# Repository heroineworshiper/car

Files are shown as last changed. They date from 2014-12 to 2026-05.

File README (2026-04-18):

3D printed truck

Copyright (C) 2012-2025 Adam Williams <broadcast at earthling dot net>

This program is free software; you can redistribute it and/or modify
it under the terms of the GNU General Public License as published by
the Free Software Foundation; either version 2 of the License, or
(at your option) any later version.

This program is distributed in the hope that it will be useful,
but WITHOUT ANY WARRANTY; without even the implied warranty of
MERCHANTABILITY or FITNESS FOR A PARTICULAR PURPOSE.  See the
GNU General Public License for more details.

You should have received a copy of the GNU General Public License
along with this program; if not, write to the Free Software
Foundation, Inc., 59 Temple Place, Suite 330, Boston, MA  02111-1307  USA

What you'll find here:

=============================================================================
3D printed truck

The current camera mounting gear is manely part of truckcam

arm_truck2.c, arm_truck2.h: the 3D printed truck firmware

settings.car: settings file that goes in /sdcard/truck/

antler3.FCStd: antlers  
    Print with .8mm nozzle .32 layer height, 20% infill
    Print in halves.  Glue a half to a tab to make a right angle.
    Then glue the other half to the right angle.

antler5.FCStd: container attachments for antlers

a1323.pcb: hall effect sensor board for motor sensor

l6234.pcb: H bridge board for motor

l6234c.FCStd: bracket which presses the L6234 board against the aluminum
heat sink/angle rod
    print with .8mm nozzle .32mm layer
    use pen spring & lock nut to press 1 side.  Use self tapper for the other side.

imu4.pcb: IMU for 3D printed truck

cring.FCStd: OBSOLETE failed retaining ring for the motors.
    .4mm nozzle
    .2mm layer height out of PETG
    no cooling fan

tire2.FCMacro: OBSOLETE generate procedural tire.
    requires creating a rigid body 1st
    .28mm layer height
    .8mm line width
    1.6mm wall thickness
    1.4mm top/bottom thickness
    100% infill
    no support
    230 printing temp
    0 bed temp
    20mm print speed
    no retraction

front_tire4.FCStd: front tire for soft TPE
    Import STL into blender
    Rename the object "Tire"
    Run helix.py to make it a helix
    Export new layers as an STL file
    .8mm nozzle.  .32 mm layer height stretched to .36 after slicing.
    The wheels must be wider to compensate for the stretching.
    left & right must be mirror images

front_wheel2.FCStd: latest front wheel
    modeled for a .4mm nozzle
    .32 layer height

glasses.FCStd: rear view glasses for testing leash mode
    .32mm layers .4 nozzle

leash13.FCStd: Latest leash enclosure
    no support for string hole
    support for base.  Melt it off.
    .2mm layers .4mm nozzle
    Ball bearings
    Use 5mV/G hall effect sensors
    Keep components near the axle to reduce inertia.

leash.c: leash firmware

leash_test.c: leash tester

light3.FCStd: nose mount for LED lightbulb

offroad2.stl: OBSOLETE offroad rear tire for hard TPU
    print with .4mm nozzle
    TPU
    .32mm layer height
    260C
    left & right must be mirror images

offroad3.stl: offroad rear tire for soft TPE
    print with .8mm nozzle 260C
    All .32mm layer height stretched to .36
    Set Z seam to "shortest" to overcome nozzle clogs 
        by printing the longest section of each layer 1st
    Print Initial layer at 10mm/s
    Buildtak bed with no heating or it won't adhere

rear_tire3.FCStd: OBSOLETE rear wheel

rear_wheel2.FCStd: OBSOLETE on-road rear wheel
    print hub cap in PLA 
        .4mm nozzle .32mm layer height for INNER HUB, INNER RING
        .4mm nozzle .2mm layer height for OUTER HUB, OUTER RING
    tire model is a mockup

rear_wheel4.FCStd: most recent off-road rear wheel
    .4mm nozzle .32mm layer height for INNER HUB, INNER RING
    .4mm nozzle .2mm layer height for OUTER HUB, OUTER RING
    change screw_r2 to select m2 or 6-32 farsteners

tire3.stl: OBSOLETE front tire for hard TPU

tire4.stl: front tire for soft TPE
    print with .8mm nozzle
    TPE
    All .32mm layer height stretched to .36mm
    260C
    left & right must be mirror images

tire6.FCMacro: Create layer for the latest rear tire
    Extrude by the layer height .32mm, then export tire.stl
    Then run helix.c to generate a helix by creating discrete layers
        ./helix tire.stl offroad3.stl
    tires must be mirror images or the truck will pull to 1 side

trailer9.FCStd: Towed drogue for aiding video composition.
    .8 nozzle .32 layers

truck_radio3.pcb: remote control TX for camera panner
    - obsolete RX

truck_radio4.pcb: remote control TX for 3D printed truck
    - obsolete RX
    - uses Si4421 for receive + Si4463 for transmit

truck4.pcb: mane board for 3D printed truck

ball_link.FCStd: 
    ball link
    100% infill
    80 deg support
    220C nozzle 0C bed to improve part cooling
    link spacing on both sides: 38.5mm
     - this grows as the wheel forks wear down
    use pliers when threading to avoid delamination
    grind a flat in the metal rod to aid the pliers
    heat the PLA & shape it with tweezers to get it to conform
    TODO: expand the opening & use heat to close it

bumper2.FCStd:
    bumper for the front of the angle rods
    print in TPU, .8 nozzle, .32 layers

container4.FCStd:
    print masks have to be booleaned with panels in Blender
    Must tweek boolean so all bits appear
    Handle doesn't attach right on the print mask seam.  It attaches 1/2 a triangle behind it.

    Use PLA, 100% infill, 220C/60C on glass
    Use .24mm on 1st 4 layers & .2 on later layers with fixcura.py.
    Ideally would use .32 on later layers.

    TODO: Create fiducials for aligning handle.
        2nd row of front mounting holes for nose.
        paper or foam gasket too fill gaps under container
        flat barrier under container

container.FCMacro:
    scripts for creating the container

corners.FCStd:
    top front corners with light positions
    print corner & support
    .4 nozzle, .2 layers 260C
    Use brim to aid adhesion to glass

lid.FCStd: container lid for waterproofing, cooling  

handle.FCStd:
    collapsing handle for the latest container & 14mm diameter carbon fiber
    print bearing + collars for camera pole or a wide collar without camera pole

rear_light2.FCStd:
    bumper for rear lights
    aluminum heat sink hangs off 2 screws
    .4 nozzle, .2 layers 260C TPU

plot.py: 
    plot steering filters

phone4.FCStd:
    wiko 3 phone

phone6.FCStd:
    moto phone holster to be printed in TPU & welded with soldering iron
    use scotch around the opening
    .4mm nozzle
    .2mm layer

radio_box3.FCStd:
    container for radio modules & switches.
    print without support
    print latches flat & glue on

speaker.FCStd: speaker holder
    .4mm .32 layers

tool.FCStd: socket wrench for 6-32 locknuts

tool2.FCStd: socket wrench for 4-40 locknuts

traction.FCMacro: create objects for traction

traction.FCStd: traction section
    .8mm nozzle, .32mm layer height, no support
    battery walls:
        print fillet side up so the laminations are the right way.
    latch pivot
    back, front, door:
        fillet on top
        support to base only, 80 degrees
    bottom, electronicals:
        no support
    right side:
        side cutout
        hinge
        captive nuts

    union for both sides (motor support | side cutout) & side mask
    union for both sides (motor support & motor mask)
    union for both sides (motor support | side cutout) & bottom mask
     - boolean error causes it to not print mirrored side.  Use cura mirror instead.
    union for both sides (motor support | side cutout) & top mask

    TODO: captive nuts for angle rod farsteners
        round all wire passages

Truck.studio2: the phone app
    Installing it requires creating /sdcard/truck & copying settings.car to it

steering.FCMacro:
    create objects for steering

steering2.FCStd: OBSOLETE steering section with 10 deg caster

steering3.FCStd: steering with 20 deg caster
    print with 0.8mm nozzle 
    .32mm layer height
    shield2
    vertical part
     - print sideways
     - ream holes with 3mm bit
    wheel mount003
    servo plate008
    bushing, bushing001
     - .4 nozzle .32mm layer
     - hard TPU
    wheel mount003

rear_wheel.FCStd: OBSOLETE motor wheel coupling
    print with 0.8mm nozzle
    .8mm line width
    .32mm layer height
    ultimaker project: front_wheel.3mf, rear_wheel.3mf
    print unions with print mask
    print rings
    no support

motor4.FCStd: motor mount
    Use 2.5mV/G hall effect sensors.
    The following use .8mm nozzle, .32 layer height, 100% infill
    SHROUD - support with 80deg overhang
        - not mirror images
    SOCK out of TPU
    CLAMPS out of PLA
    MOTOR PLATE - no support, PETG

    SENSOR PLATE
        100% infill
        .4mm nozzle, .2mm layer
    MAGNET HOLDER
        PETG
        no support, 100% infill
        .4mm nozzle .32mm layer
        Heat to thread set crew & fit magnet
    GASKET:
        TPU .4mm nozzle .32mm layer

car_remote.FCMacro:
    create objects for car_remote & cam_remote

car_remote4.FCStd: remote control for vehicle
    Use 2.5mV/G hall effect sensors
    disable support for the top & bottom
    use support only for the joysticks
    no ironing
    .4mm nozzle
    .6mm top/bottom thickness
    1.2mm wall thickness
    skirt
    use timelapse mode to improve columns
    bottom, top:
        expand all clones
        select base of mirror
        select visible objects
        no support
        print with outside facing the bed
    steering pivot, throttle pivot:
        use support from magnet holder to bed
        Z seem on thicker walls
    steering lever, throttle lever:
        flat side down
    covers for power, increase speed, decrease speed:
        no support
        with wide part facing bed
    sock top/bottom: must clean the inside before welding

car_remote.X: remote control firmware

arm_receiver.c: oversampling, high quality receiver

charger3.FCStd: charging stand for a Qi charger
    print with .4mm nozzle, .4mm line width, no support
    M2 self tappers

confuser.FCStd: jetson nano enclosure

nose2.FCStd: nose cone
    print with .8mm nozzle, .20mm layers on glass
    raise & lower print mask Z to subdivide the top panel
nose.FCMacro: create isogrids for the nose cone

filament budget for traction module:
motor mounts: 39g * 2
bottom: 55g
sides: 49g * 2
front, rear, door, battery walls:  55g

===========================================================================

Carbon fiber farsteners for a fixed gopro

Key files:

isogrid_plane.FCMacro:
    create isogrids for cam_remote, car_remote, & cam_gearbox.FCStd

clamshell.FCMacro:
    create walls for cam_remote, car_remote OBSOLETE

gopro_case2.FCStd: case for a gopro 7
    collars, interfaces for CF rod
    print with support everywhere, lesser overhangs facing up
    skirt adhesion
    .2mm layers .4mm nozzle

gopro.FCStd
    top endpiece for carbon fiber
        print with laminations distributing plasic flex along right angles
        support everywhere
    
    bottom endpiece

    both endpieces need "outer shroud" + "bolt loop"
        print with laminations perpendicular to shaft
    
    4 * "inner shroud slice" for the top & bottom endpieces
        print with laminations distributing plastic flex along curves

    bottom needs "base"
    
    top needs "cam"

=============================================================================

Camera panning mount:

This is used together with countreps to get automatic tracking, motion
control.

arm_cam.c: camera motor receiver using STM32.
    Build with make cam.bin
    Uses a brushless servo hacked into a stepper motor with the servo/ firmware.

arm_cam.c.l6234: camera motor receiver using an L6234 
    to drive a stepper motor.

cam_remote.pcb, cam.pcb: electronicals

cam_remote.X: camera remote control firmware
    Build with mplab_ide

cam_gearbox.FCStd: OBSOLETE
    hobby motor as a stepper motor
    4.5:1 gear reduction for panning motor
    walls have to be printed with .4mm thick tops & bottoms
        to get smooth surfaces
    print pinion with gear on bottom & no support
    install pinion with hex facing motor hex

cam_remote2.FCStd:
    TODO: 5mm longer for new battery
        guard for power switch

    remote control for camera panner
    no ironing
    no horizontal expansion
    .4mm nozzle
    .8mm top/bottom thickness
    1.2mm wall thickness
    support with 60 deg overhang angle
    skirt
    60C bed temp
    support to bed only except for top & bottom
    top, bottom:
        block support over all except edges with switch covers
        print with outside facing the bed
        .8mm top & bottom thickness to get smooth 2mm sheets
        print top with spring holder but not spring
    lever, steering:
        print with support on flatter side
        don't print magnets
    power, increase, decrease cover:
        print with no support
    top switch cover, bottom switch cover:
        support everywhere

gopro_rightangle.FCStd: OBSOLETE handle end pieces
    cf collar - print 2 for the handle
        100% infill

    solid right angle coupling between 2 carbon fiber rods
    print with no support
    print with laminations distributing plastic flex along curves

    attachment + attachment mirror are required

gopro_motor.FCStd: OBSOLETE
    coupling of CF to direct drive motor for panning without a gearbox
    must print with
        4 * "inner shroud slice"
         - TODO: make hole for motor shaft & make base wider to compensate for lost material
        "outer shroud" + "bolt loop"

servo/:
    Firmware for turning a brushless TS-940-HG servo into a stepper motor.
    The project file is servo/motor.wsp.  The output hex file is servo/motor.hex.
    Must be built with the silabs IDE & flashed with the blheli tool.
    https://www.silabs.com/developers/8-bit-8051-microcontroller-software-studio
    http://www.olliw.eu/2012/owsilprog/#firmware

shroud.FCStd: OBSOLETE
    the shroud for a direct drive panning motor
    tube segment was created with 
    ./tube shroud.stl 30 60 0 16
    print with .4mm line width
    205C filament 60C bed

15mph/1185rpm on 12V with no load
4248 traction motors with 108mm tires:
20 turns 26 AWG

272rpm on 10V with no load
70 turns * 32 AWG

Maximum windings: 25 turns * 26AWG
75 turns * 32 AWG

RPM = C constant * V voltage * A wire cross section

========================================================================
OBSOLETE files:

arm_car.c: 2 wheel robot driven by direct drive, sensored brushless motors

arm_cc1101.c: 433Mhz radio library for the ARM

arm_truck.c, arm_truck.h: the lunchbox firmware

arm_xbee.c: xbee library for the ARM

car.s: vehicle firmware for the G buggy

car_remote.s: orginal assembly language remote for CC1101 & XBee

car_remote.X: 3D printed vehicle remote control

car_receive.X: low quality RS232 receiver

car_remote.X.bak: failed remote for the XBee with frequency hopping

freq_hops.ods: frequency hopping plot to aid in spreading the frequencies

fuse.X: a software fuse for testing motors

truck3.pcb: last layout for the tamiya board

uwb.X, dw3000.pcb, dw3220.fp, uwb_test.c: failed UWB experiment with the
DW3221

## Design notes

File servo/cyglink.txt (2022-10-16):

"Z:\servo\motor.obj"  TO "Z:\servo\motor" RS(256) PL(68) PW(78)

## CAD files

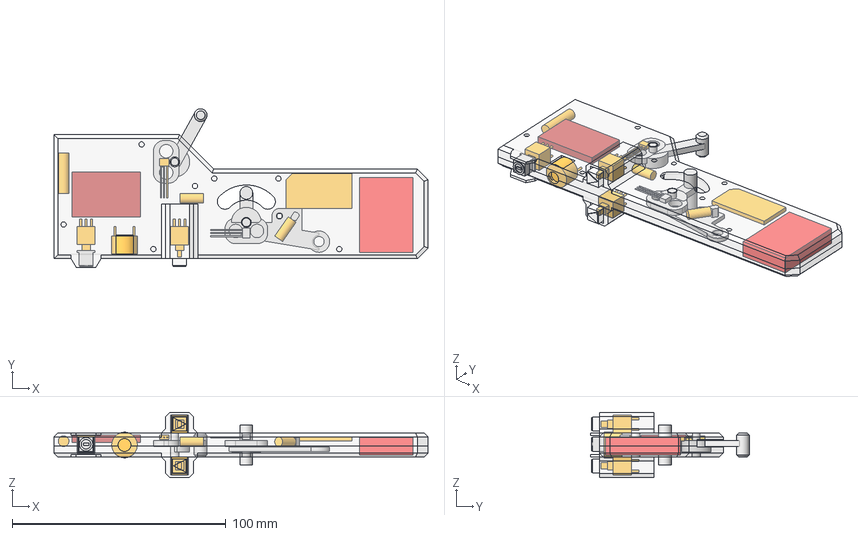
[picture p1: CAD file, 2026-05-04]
car_remote4.FCStd
175.0 x 74.2 x 30.6 mm
rect
wheel shaft
handle
lever opposition
magnet holder001
radio
wheel shaft001
lever opposition001
magnet holder003
wheel shaft002
spring003
up icon
switch cover
down icon
switch cover001
power switch001
down button
up button
decrease speed cover001
hall
top001
bottom001
hall001
speaker001
power switch cap002
throttle lever pivot002
increase speed cover (Mirror #6)
steering lever pivot001
spring
battery001
inductor (X set by charger clearance)
charger board001
antenna (clear from inductor)001

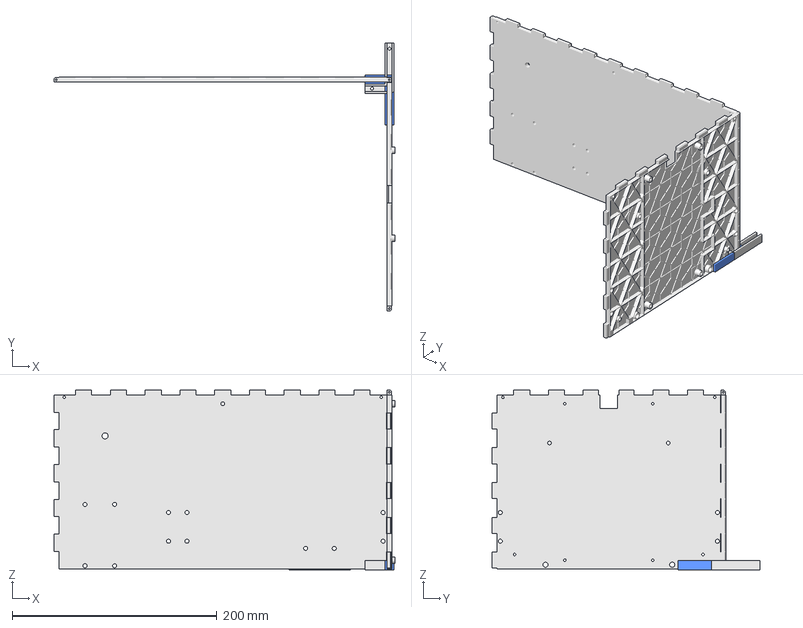
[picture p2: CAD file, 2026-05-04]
rear_light2.FCStd
333.4 x 261.6 x 175.7 mm
rear corner
Body (Mirror #2)
side

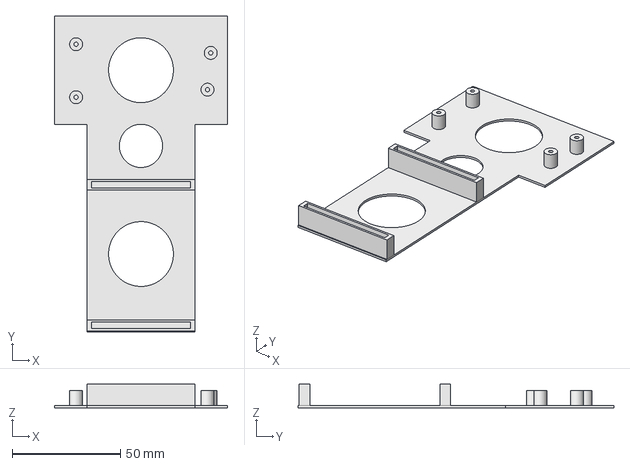
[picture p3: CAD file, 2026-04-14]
charger3.FCStd
80.0 x 146.0 x 11.0 mm

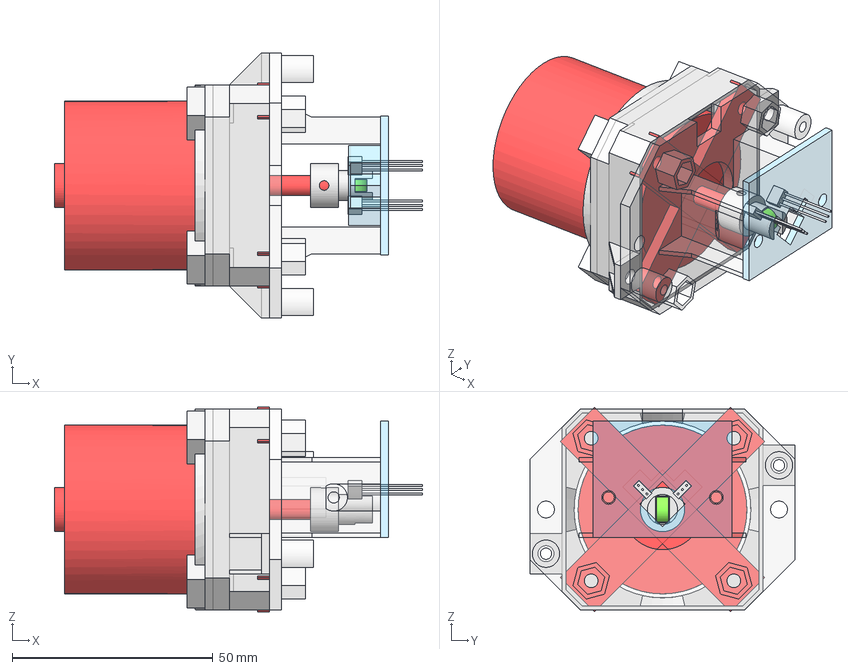
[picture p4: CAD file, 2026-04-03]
motor4.FCStd
91.6 x 66.0 x 50.9 mm
motor
sensor plate003
magnet004
gasket
clamps
shroud001
firewall
halls
magnet holder

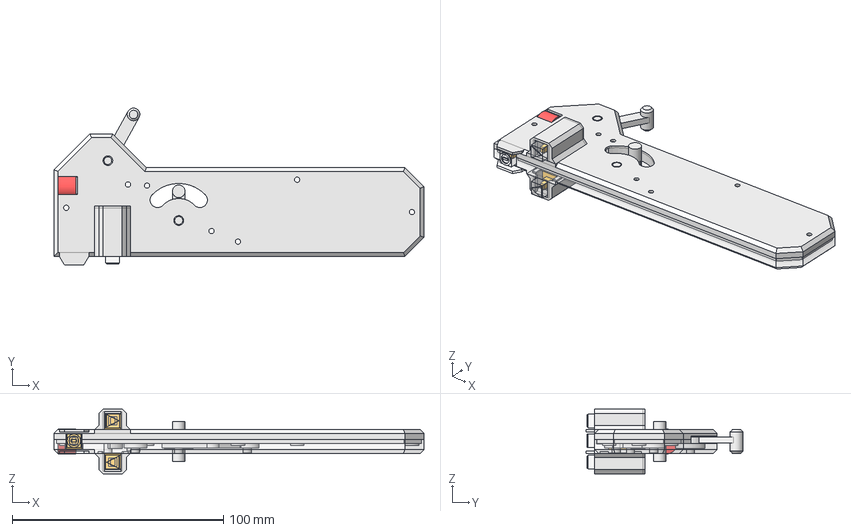
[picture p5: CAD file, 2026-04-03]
car_remote3.FCStd
175.0 x 74.2 x 30.6 mm
hinge
spring stop001
rect
wheel shaft
handle
lever opposition
magnet holder001
wheel shaft001
lever opposition001
magnet holder003
wheel shaft002
spring003
hinge001
spring stop002
spring004
power icon001
power switch cover
up icon
switch cover
down icon
switch cover001
speaker
speaker pin001
speaker pin
power switch001
down button
up button
decrease speed cover001
increase speed cover001
hall
top001
bottom001
hall001

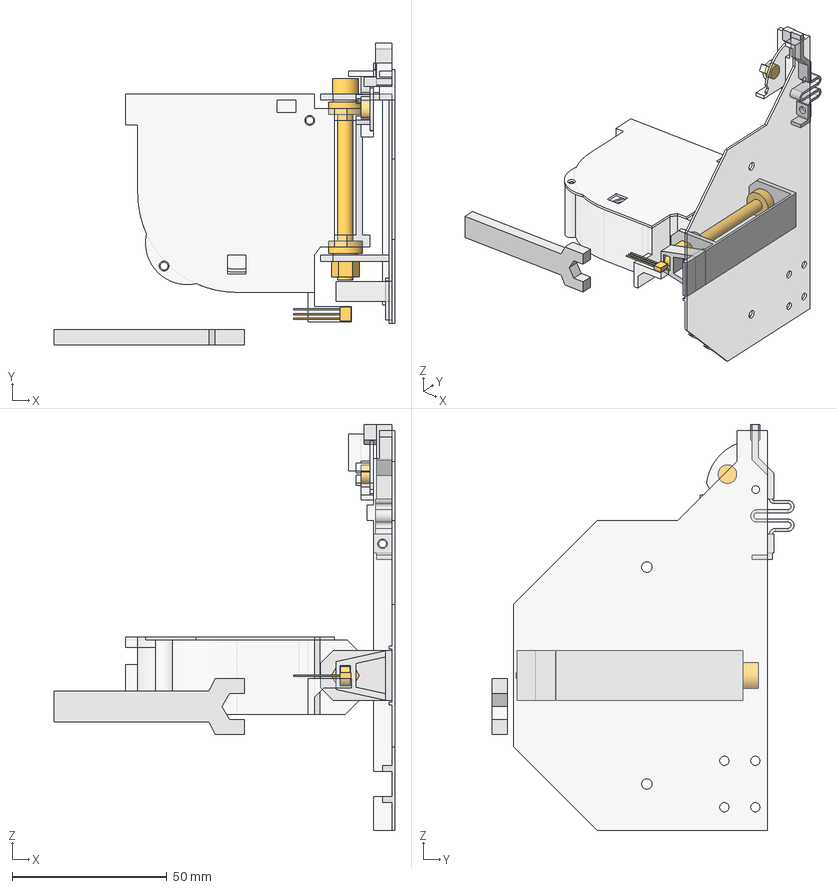
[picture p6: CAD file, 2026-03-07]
leash13.FCStd
110.0 x 97.5 x 131.0 mm
panel
hall006
bearing001
bearing002
bolt001
nut001
magnet
base005
cover001
frame001
latch002
magnet holder002
magnet001
spring
wrench

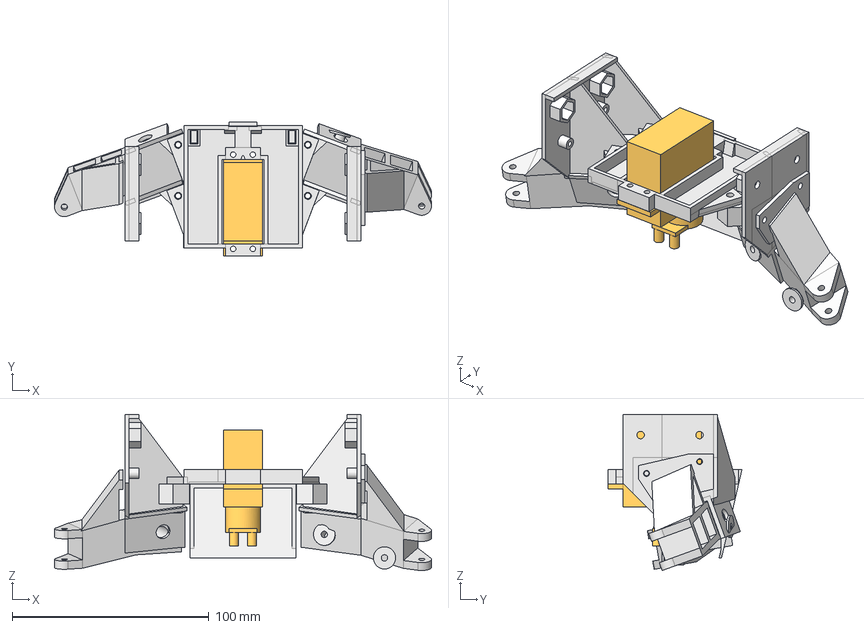
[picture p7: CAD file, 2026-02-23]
steering3.FCStd
191.8 x 68.2 x 79.4 mm
servo
wheel vertical mirror001
wheel fork006
wheel stopper001 (Mirror #11)
shield2
angle rod002
bushing
bushing001
wheel mount003
bushing002
bushing003
servo plate008

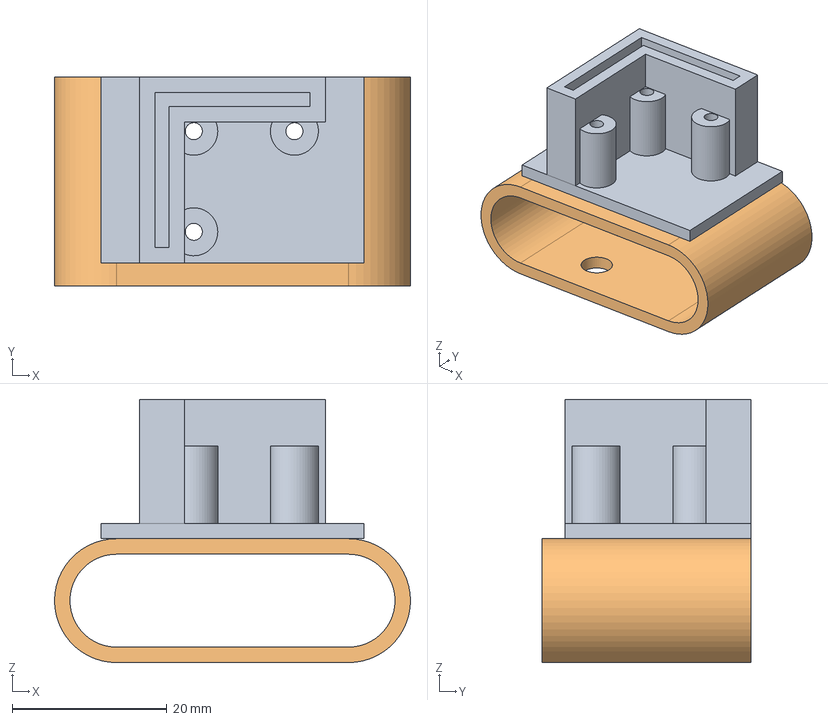
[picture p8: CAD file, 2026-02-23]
bumper2.FCStd
46.0 x 27.0 x 34.0 mm
glove003
bumper003

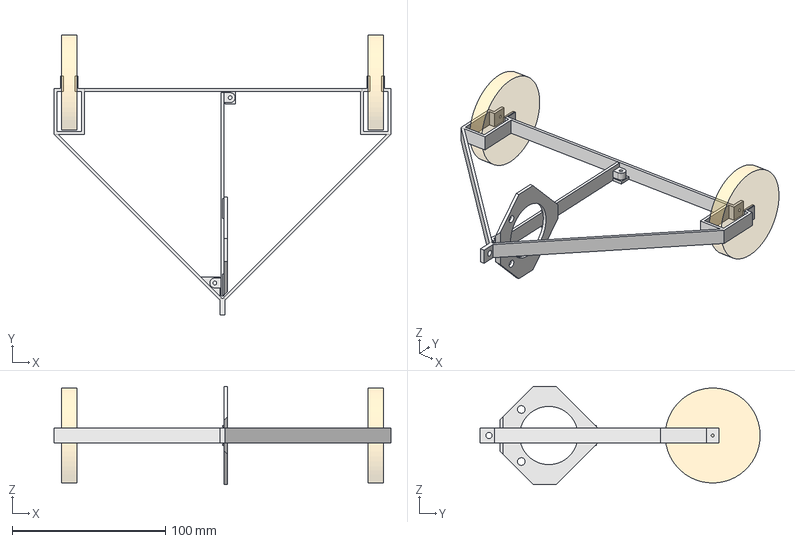
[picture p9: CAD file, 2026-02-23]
trailer9.FCStd
220.0 x 183.0 x 64.0 mm
wheel001
wheel002
frame
skid
center

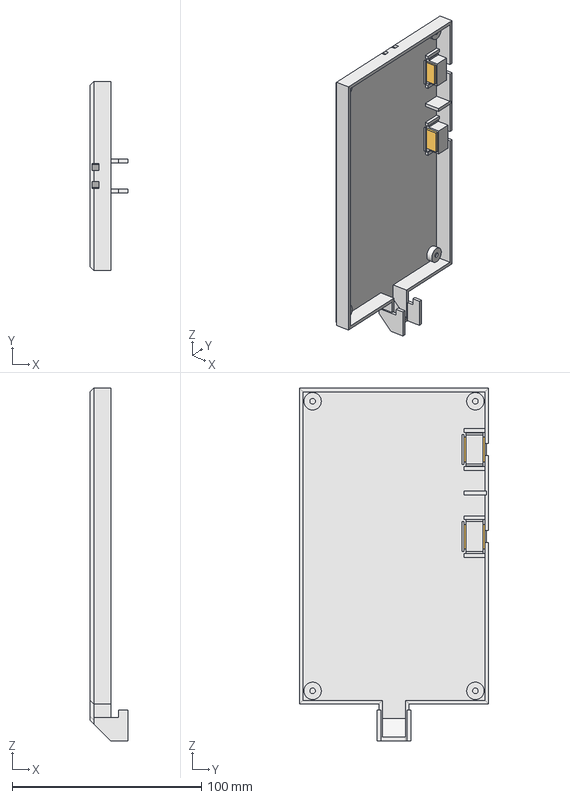
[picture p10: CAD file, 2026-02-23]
radio_box3.FCStd
20.0 x 100.0 x 186.5 mm
radio_box
switches001
strap
strap001
stringer031
latch002
latch001 (Mirror #1)

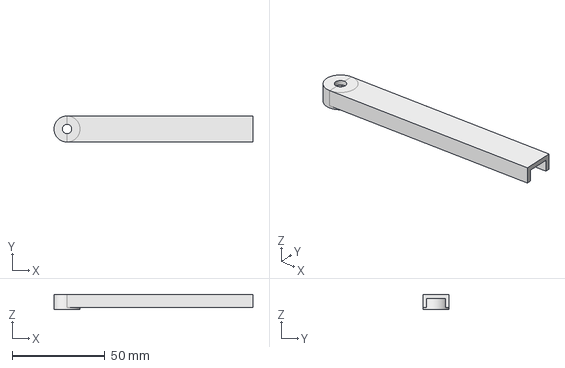
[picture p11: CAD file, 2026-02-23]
tool.FCStd
107.0 x 14.0 x 8.00 mm

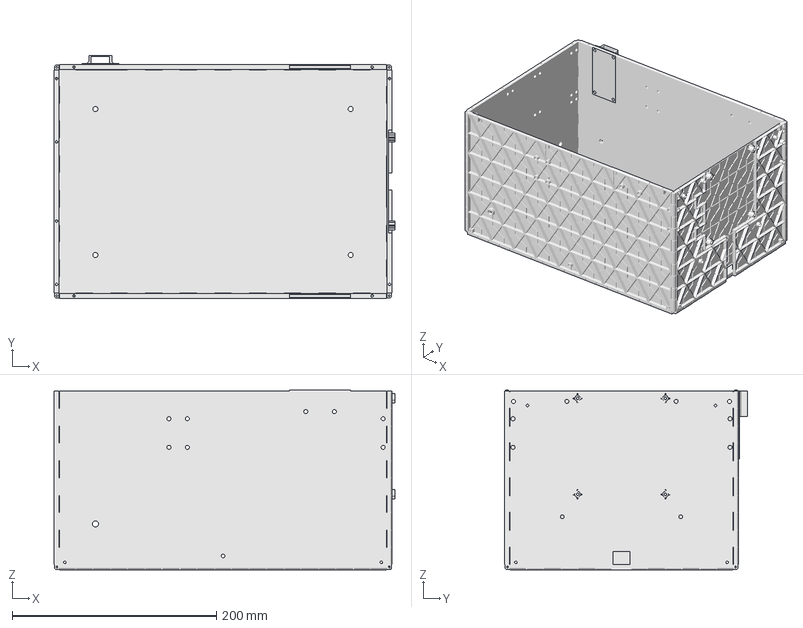
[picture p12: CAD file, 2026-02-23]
antler5.FCStd
334.0 x 238.0 x 176.0 mm
doubler001
panel
hook
container3

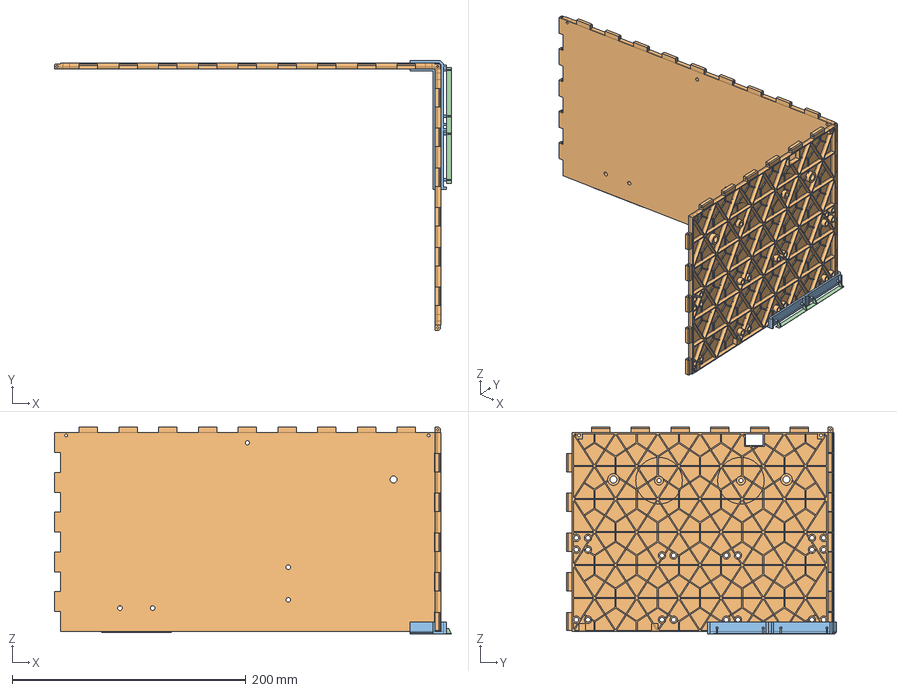
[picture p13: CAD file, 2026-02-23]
corners.FCStd
339.6 x 230.6 x 176.7 mm
corner
support004

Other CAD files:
cam_remote.X/dist/default/production/cam_remote.X.production.obj
servo/motor.OBJ
cam_remote.X/dist/default/production/cam.X.production.obj
servo/motor.c.step
servo/F330_Blinky.OBJ
antler.FCStd
antler2.FCStd
antler3.FCStd
antler4.FCStd
ball_link.FCStd
bottom_corner.FCStd
bumper.FCStd
cam_gearbox.FCStd
cam_remote.FCStd
cam_remote2.FCStd
car_remote.FCStd
car_remote2.FCStd
charger.FCStd
charger2.FCStd
confuser.FCStd
connector.FCStd
corners2.FCStd
cring.FCStd
extruder.FCStd
front_corner2.stl
front_tire.FCStd
front_tire2.FCStd
front_tire3.FCStd
front_tire4.FCStd
front_wheel.FCStd
front_wheel2.FCStd
glasses.FCStd
gopro.FCStd
gopro_case.FCStd
gopro_case2.FCStd
gopro_motor.FCStd
gopro_rightangle.FCStd
handle.FCStd
isogrid_test.FCStd
knob.FCStd
l6234.FCStd
l6234b.FCStd
l6234c.FCStd
leash11.FCStd
leash4.FCStd
leash5.FCStd
leash8.FCStd
leash9.FCStd
lid.FCStd
light.FCStd
light2.FCStd
light3.FCStd
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

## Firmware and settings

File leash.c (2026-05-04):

/*
 * Smart leash
 * Copyright (C) 2022-2025 Adam Williams <broadcast at earthling dot net>
 * 
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
 */

// Plug in the ISP programmer
// make leash.hex
// make leash_fuse
// make leash_isp

// Arduino ISP to leash:
// GND - GND
// 13 - CLK
// 12 - MISO
// 11 - MOSI
// 10 - RESET


#define F_CPU 8000000L

#include <stdint.h>
#include <inttypes.h>
#include <avr/io.h>
#include <avr/pgmspace.h>
#include <avr/interrupt.h>
#include <avr/wdt.h>

#define HZ 125
#define FRACTION 256
#define LED_ON PORTB &= ~(1 << PORTB5);
#define LED_OFF PORTB |= (1 << PORTB5);
#define LED_TOGGLE PORTB ^= (1 << PORTB5);
#define LED_DOWNSAMPLE 15

#define BAUD 115200L

#define ENCODER_CENTER 128
#define ENCODER_THRESHOLD 8
#define ON_THRESHOLD 100

#define ENCODER_START 0
#define ENCODER0_LOW 1
#define ENCODER1_LOW 2
#define ENCODER0_HIGH 3
#define ENCODER1_HIGH 4
int8_t encoder_state = ENCODER_START;
int8_t prev_encoder = ENCODER_START;
int16_t encoder_counts = 0;
uint8_t debug_count = 0;

uint16_t enable_accum = 0;
uint16_t encoder0_accum = 0;
uint16_t encoder1_accum = 0;
uint16_t angle_accum = 0;
uint8_t enable_adc = 0;
uint8_t encoder0_adc = 0;
uint8_t encoder1_adc = 0;
uint16_t angle_adc = 0;
uint8_t encoder_count = 0;
uint8_t angle_count = 0;
uint8_t enable_count = 0;
#define ENCODER_OVERSAMPLE 1
#define POT_OVERSAMPLE 32
#define ENABLE_OVERSAMPLE 32
uint8_t tick;
uint8_t led_count = 0;

// byte stuffing for UART
#define START_CODE 0xff
#define ESC_CODE 0xfe

#define UART_SIZE 64
uint8_t uart_buffer[UART_SIZE];
uint8_t uart_used = 0;
uint8_t uart_write_ptr = 0;
uint8_t uart_read_ptr = 0;

#define bitRead(value, bit) (((value) >> (bit)) & 0x01)
#define bitSet(value, bit) ((value) |= (1UL << (bit)))
#define bitToggle(value, bit) ((value) ^= (1UL << (bit)))
#define bitClear(value, bit) ((value) &= ~(1UL << (bit)))
#define bitWrite(value, bit, bitvalue) (bitvalue ? bitSet(value, bit) : bitClear(value, bit))

#define CLAMP(x, y, z) ((x) = ((x) < (y) ? (y) : ((x) > (z) ? (z) : (x))))
#define MAX(x, y) ((x) > (y) ? (x) : (y))
#define MIN(x, y) ((x) < (y) ? (x) : (y))
#define ABS(x) ((x) < 0 ? (-(x)) : (x))



// send data to the UART buffer
void send_uart(uint8_t *text, uint8_t size)
{
	uint8_t i;
	for(i = 0; uart_used < UART_SIZE && i < size; i++)
	{
		uart_buffer[uart_write_ptr++] = text[i];
		uart_used++;
		if(uart_write_ptr >= UART_SIZE) uart_write_ptr = 0;
	}
}

void send_uart1(uint8_t c)
{
    if(uart_used < UART_SIZE)
    {
        uart_buffer[uart_write_ptr++] = c;
	    uart_used++;
	    if(uart_write_ptr >= UART_SIZE) uart_write_ptr = 0;
    }
}

void print_text(char *text)
{
	uint8_t i;
	for(i = 0; uart_used < UART_SIZE && text[i] != 0; i++)
	{
		uart_buffer[uart_write_ptr++] = text[i];
		uart_used++;
		if(uart_write_ptr >= UART_SIZE) uart_write_ptr = 0;
	}
}

void print_number_nospace(int number)
{
	char string[8];
	char *ptr = string;
	if(number < 0)
	{
		*ptr++ = '-';
		number = -number;
	}

	if(number >= 10000) *ptr++ = '0' + (number / 10000);
	if(number >= 1000) *ptr++ = '0' + ((number / 1000) % 10);
	if(number >= 100) *ptr++ = '0' + ((number / 100) % 10);
	if(number >= 10) *ptr++ = '0' + ((number / 10) % 10);
	*ptr++ = '0' + (number % 10);
	*ptr = 0;
	print_text(string);
}

void print_number(int number)
{
    print_number_nospace(number);
	print_text(" ");
}


void print_fixed(int16_t number)
{
    print_number_nospace(number / FRACTION);
	char string[8];
	if(number < 0) number = -number;
    uint8_t fraction = number % FRACTION;
    string[0] = '.';
    fraction = fraction * 100 / FRACTION;
    string[1] = '0' + (fraction / 10);
    string[2] = '0' + (fraction % 10);
    string[3] = ' ';
    string[4] = 0;
	print_text(string);
}


void encode_serial(uint8_t c)
{
    if(c == START_CODE || c == ESC_CODE)
    {
        send_uart1(ESC_CODE);
        send_uart1(0xff ^ c);
    }
    else
        send_uart1(c);
}

void encode_start()
{
    send_uart1(START_CODE);
}

void handle_serial()
{
	if(uart_used) 
	{
	    if(bitRead(UCSR0A, UDRE0)) 
	    {
			bitSet(UCSR0A, UDRE0); 
			UDR0 = uart_buffer[uart_read_ptr++]; 
			if(uart_read_ptr >= UART_SIZE) uart_read_ptr = 0; 
			uart_used--; 
	    }
	}
}

void init_serial()
{
	uint16_t baud_setting = (F_CPU / 4 / BAUD - 1) / 2;
	UBRR0H = baud_setting >> 8;
	UBRR0L = baud_setting & 0xff;
	UCSR0A = (1 << U2X0);
	UCSR0C = (1 << UCSZ01) |
		(1 << UCSZ00);
	UCSR0B = (1 << RXCIE0) |
		(1 << TXEN0);
//         |
//		(1 << RXEN0);
}



void handle_encoder()
{
    if(encoder1_adc <= ENCODER_CENTER - ENCODER_THRESHOLD)
    {
        encoder_state = ENCODER1_LOW;
    }
    else
    if(encoder1_adc >= ENCODER_CENTER + ENCODER_THRESHOLD)
    {
        encoder_state = ENCODER1_HIGH;
    }
    else
    if(encoder0_adc <= ENCODER_CENTER - ENCODER_THRESHOLD)
    {
        encoder_state = ENCODER0_LOW;
    }
    else
    if(encoder0_adc >= ENCODER_CENTER + ENCODER_THRESHOLD)
    {
        encoder_state = ENCODER0_HIGH;
    }
    
    if(encoder_state != prev_encoder)
    {
        if(prev_encoder == ENCODER1_LOW && encoder_state == ENCODER0_LOW ||
            prev_encoder == ENCODER0_LOW && encoder_state == ENCODER1_HIGH ||
            prev_encoder == ENCODER1_HIGH && encoder_state == ENCODER0_HIGH ||
            prev_encoder == ENCODER0_HIGH && encoder_state == ENCODER1_LOW)
            encoder_counts++;
        else
        if(prev_encoder == ENCODER0_LOW && encoder_state == ENCODER1_LOW ||
            prev_encoder == ENCODER1_LOW && encoder_state == ENCODER0_HIGH ||
            prev_encoder == ENCODER0_HIGH && encoder_state == ENCODER1_HIGH ||
            prev_encoder == ENCODER1_HIGH && encoder_state == ENCODER0_LOW)
            encoder_counts--;

        prev_encoder = encoder_state;
    }
}

void main()
{
// disable watchdog
	WDTCSR = 0;
	init_serial();
	print_text("\n\nWelcome to smart leash\n");

// LED/DEBUG
    DDRB |= 1 << DDB5;
    LED_ON

// tick clock prescaler page 108
// CLKio is 32khz
    TCCR0B = 0b00000100;

#define ADMUX_BASE 0b01000000
    ADMUX = ADMUX_BASE;
    ADCSRA = 0b10000111;
// disable digital inputs
    DIDR0 = 0b00001111;
    bitSet(ADCSRA, ADSC);

// enable interrupts
	sei();

 	while(1)
	{
		handle_serial();

// handle tick
        if(bitRead(TIFR0, TOV0))
        {
            bitSet(TIFR0, TOV0);
            tick++;
            if(tick >= HZ / 25)
            {
                tick = 0;
            }
        }

        if(bitRead(ADCSRA, ADIF))
        {
            uint8_t channel = ADMUX & 0xf;
            bitSet(ADCSRA, ADIF);
            
// must read the right byte order to update the registers
            uint8_t low = ADCL;
            uint8_t high = ADCH;
            switch(channel)
            {
                case 0:
                    ADMUX = ADMUX_BASE | 1;
                    encoder0_accum += (high << 8) | low;
                    bitSet(ADCSRA, ADSC);
                    break;
                case 1:
                    ADMUX = ADMUX_BASE | 2;
                    encoder1_accum += (high << 8) | low;
                    bitSet(ADCSRA, ADSC);
                    encoder_count++;

                    if(encoder_count >= ENCODER_OVERSAMPLE)
                    {
                        encoder0_adc = encoder0_accum / ENCODER_OVERSAMPLE / 4;
                        encoder1_adc = encoder1_accum / ENCODER_OVERSAMPLE / 4;
                        encoder_count = 0;
                        encoder0_accum = 0;
                        encoder1_accum = 0;


                        handle_encoder();

//                         debug_count++;
//                         if(debug_count > 10)
//                         {
//                             debug_count = 0;
//                         print_number(encoder0_adc);
//                         print_number(encoder1_adc);
//                         print_number(angle_adc);
//                         print_text("\n");
//                        }
                    }
                    break;
                case 2:
                    ADMUX = ADMUX_BASE | 3;
                    angle_accum += (high << 8) | low;
                    bitSet(ADCSRA, ADSC);

                    angle_count++;
                    if(angle_count >= POT_OVERSAMPLE)
                    {
// scale it to maximize resolution
//                        angle_accum -= 32 * 512;
//                        angle_accum /= POT_OVERSAMPLE;
//                        angle_accum += 128;
// send the entire accumulator
                        angle_adc = angle_accum;
// compress accumulator into 8 bits
//                        angle_adc = angle_accum / POT_OVERSAMPLE / 4;
                        angle_accum = 0;
                        angle_count = 0;

// send to autopilot
                        if(enable_adc >= ON_THRESHOLD)
                        {
                            LED_TOGGLE

                            encode_start();
                            encode_serial(encoder_counts & 0xff);
                            encode_serial(encoder_counts >> 8);
// send the entire accumulator
                            encode_serial(angle_adc & 0xff);
                            encode_serial(angle_adc >> 8);
                            encode_serial(encoder0_adc);
                            encode_serial(encoder1_adc);
                        }
                        else
                        {
// standby
                            encoder_counts = 0;
                            led_count++;
                            if(led_count >= LED_DOWNSAMPLE)
                            {
                                led_count = 0;
                                LED_TOGGLE
                            }
                        }
                    }
                    break;

                case 3:
                    ADMUX = ADMUX_BASE;
                    enable_accum += (high << 8) | low;
                    bitSet(ADCSRA, ADSC);
                    enable_count++;

                    if(enable_count >= ENABLE_OVERSAMPLE)
                    {
                        enable_adc = enable_accum / ENABLE_OVERSAMPLE / 4;
                        enable_accum = 0;
                        enable_count = 0;

// lion readable output
                        print_text("DEBUG: ");
                        print_number(enable_adc);
                        print_number(angle_adc);
                        print_number(encoder0_adc);
                        print_number(encoder1_adc);
                        print_number(encoder_counts);
                        print_text("\n");
                    }
                    break;
            }
        }
    }
}

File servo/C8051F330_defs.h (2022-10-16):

//-----------------------------------------------------------------------------
// C8051F330_defs.h
//-----------------------------------------------------------------------------
// Copyright 2007, Silicon Laboratories, Inc.
// http://www.silabs.com
//
// Program Description:
//
// Register/bit definitions for the C8051F33x family.
// **Important Note**: The si_toolchain.h header file should be included
// before including this header file.
//
// Target:         C8051F330, 'F331, 'F333, 'F334, 'F335
// Tool chain:     Generic
// Command Line:   None
//
// Release 1.4 - 20 AUG 2012 (TP)
//    -Added #define for _XPAGE to provide support for SDCC memory paging
//     (pdata)
// Release 1.3 - 07 AUG 2007 (PKC)
//    -Removed #include "si_toolchain.h". The C source file should include it.
//    -Removed FID and fixed formatting.
// Release 1.2 - 29 SEP 2006 (PKC)
//    -Reformatted header file to enable portable SFR definitions
// Release 1.1 - 11 JAN 2006 (GP)
//    -Converted file to new coding guidelines
//    -Added #defines for interrupt priorities
//    -Added #ifndef/#define to allow multiple includes of file
// Release 1.0
//    -Latest release before new firmware coding standard

//-----------------------------------------------------------------------------
// Header File Preprocessor Directive
//-----------------------------------------------------------------------------

#ifndef C8051F330_DEFS_H
#define C8051F330_DEFS_H

//-----------------------------------------------------------------------------
// Byte Registers
//-----------------------------------------------------------------------------

SI_SFR(P0, 0x80);                        // Port 0 Latch
SI_SFR(SP, 0x81);                        // Stack Pointer
SI_SFR(DPL, 0x82);                       // Data Pointer Low
SI_SFR(DPH, 0x83);                       // Data Pointer High
SI_SFR(PCON, 0x87);                      // Power Control
SI_SFR(TCON, 0x88);                      // Timer/Counter Control
SI_SFR(TMOD, 0x89);                      // Timer/Counter Mode
SI_SFR(TL0, 0x8A);                       // Timer/Counter 0 Low
SI_SFR(TL1, 0x8B);                       // Timer/Counter 1 Low
SI_SFR(TH0, 0x8C);                       // Timer/Counter 0 High
SI_SFR(TH1, 0x8D);                       // Timer/Counter 1 High
SI_SFR(CKCON, 0x8E);                     // Clock Control
SI_SFR(PSCTL, 0x8F);                     // Program Store R/W Control
SI_SFR(P1, 0x90);                        // Port 1 Latch
SI_SFR(TMR3CN, 0x91);                    // Timer/Counter 3 Control
SI_SFR(TMR3RLL, 0x92);                   // Timer/Counter 3 Reload Low
SI_SFR(TMR3RLH, 0x93);                   // Timer/Counter 3 Reload High
SI_SFR(TMR3L, 0x94);                     // Timer/Counter 3 Low
SI_SFR(TMR3H, 0x95);                     // Timer/Counter 3 High
SI_SFR(IDA0L, 0x96);                     // Current Mode Dac0 Low
SI_SFR(IDA0H, 0x97);                     // Current Mode Dac0 High
SI_SFR(SCON0, 0x98);                     // UART0 Control
SI_SFR(SBUF0, 0x99);                     // UART0 Data Buffer
SI_SFR(CPT0CN, 0x9B);                    // Comparator0 Control
SI_SFR(CPT0MD, 0x9D);                    // Comparator0 Mode Selection
SI_SFR(CPT0MX, 0x9F);                    // Comparator0 Mux Selection
SI_SFR(P2, 0xA0);                        // Port 2 Latch
SI_SFR(SPI0CFG, 0xA1);                   // SPI0 Configuration
SI_SFR(SPI0CKR, 0xA2);                   // SPI0 Clock Rate Control
SI_SFR(SPI0DAT, 0xA3);                   // SPI0 Data
SI_SFR(P0MDOUT, 0xA4);                   // Port 0 Output Mode Configuration
SI_SFR(P1MDOUT, 0xA5);                   // Port 1 Output Mode Configuration
SI_SFR(P2MDOUT, 0xA6);                   // Port 2 Output Mode Configuration
SI_SFR(IE, 0xA8);                        // Interrupt Enable
SI_SFR(CLKSEL, 0xA9);                    // Clock Select
SI_SFR(EMI0CN, 0xAA);                    // External Memory Interface Control
SI_SFR(OSCXCN, 0xB1);                    // External Oscillator Control
SI_SFR(OSCICN, 0xB2);                    // Internal Oscillator Control
SI_SFR(OSCICL, 0xB3);                    // Internal Oscillator Calibration
SI_SFR(FLSCL, 0xB6);                     // Flash Scale
SI_SFR(FLKEY, 0xB7);                     // Flash Lock And Key
SI_SFR(IP, 0xB8);                        // Interrupt Priority
SI_SFR(IDA0CN, 0xB9);                    // Current Mode DAC0 Control
SI_SFR(AMX0N, 0xBA);                     // AMUX0 Negative Channel Select
SI_SFR(AMX0P, 0xBB);                     // AMUX0 Positive Channel Select
SI_SFR(ADC0CF, 0xBC);                    // ADC0 Configuration
SI_SFR(ADC0L, 0xBD);                     // ADC0 Low
SI_SFR(ADC0H, 0xBE);                     // ADC0 High
SI_SFR(SMB0CN, 0xC0);                    // SMBus0 Control
SI_SFR(SMB0CF, 0xC1);                    // SMBus0 Configuration
SI_SFR(SMB0DAT, 0xC2);                   // SMBus0 Data
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

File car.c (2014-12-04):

// mane board for passively stable 2 wheeler


// 18f1320
// usb_programmer -p 18f1320 -e
// usb_programmer -p 18f1320 -c 0x300000 1100100000000000
// Internal oscillator
// usb_programmer -p 18f1320 -c 0x300002 0001111100001010
// brownout protection
// usb_programmer -p 18f1320 -c 0x300006 0000000010000001
// low voltage programming disabled
// make car
// usb_programmer -p 18f1320 -z 0 car.hex
// usb_programmer -p 18f1320 -z 0  -r car.hex

// if it randomly crashes, reflash it








#include <pic18fregs.h>
#include <stdint.h>
#include "util.h"

#define CLOCKSPEED 8000000
#define BUFFER_SIZE 8
#define BAUD 9600
// clock jitter is keeping it as low as possible
//#define BAUD_RATE_CODE (CLOCKSPEED / (BAUD * 4) - 1)
#define BAUD_RATE_CODE 208
#define SYNC_CODE 0xe5
#define THROTTLE_PERIOD 32767
// multiply gyro output by this to get steering feedback
//#define AUTO_STEERING_GAIN 4
#define AUTO_STEERING_GAIN 1
// limit for auto steering magnitude
//#define AUTO_STEERING_LIMIT STEERING_PERIOD / 4
#define AUTO_STEERING_LIMIT STEERING_PERIOD / 2
// integral step
#define STEERING_I_STEP 32
#define STEERING_I_LIMIT STEERING_PERIOD / 4
//#define STEERING_I_LIMIT STEERING_PERIOD / 2
// total readings to use for the center calculation
#define GYRO_TOTAL 1024
// maximum range for center calculation
#define GYRO_LIMIT 128
// timer for LED flashing
#define LED_DELAY 64
// timer for packet flashing
#define LED_DELAY2 2
// total readings for each GYRO_RESULT
#define GYRO_OVERSAMPLE_TOTAL 32
// amount heading has to be off to command auto steering voltage
//#define HEADING_DEADBAND 0x0100
#define HEADING_DEADBAND 0x0000
// amount user changes heading in each packet
#define HEADING_CHANGE 0x0200
// enable UART output
//#define DEBUG

// analog range
#define STEERING_MID 0x8000
// deadband
#define STEERING_MIN 0x800
#define STEERING_MAX 0x7f00

#define THROTTLE_MIN 0x100
#define THROTTLE_MAX 0xff00

#define SDO_LAT LATAbits.LATA2
#define SDO_TRIS TRISAbits.TRISA2

#define SCK_LAT LATAbits.LATA3
#define SCK_TRIS TRISAbits.TRISA3

#define CS0_LAT LATBbits.LATB5
#define CS0_TRIS TRISBbits.TRISB5

#define LEFT_FWD_LAT LATBbits.LATB3
#define LEFT_FWD_TRIS TRISBbits.TRISB3
#define LEFT_BWD_LAT LATAbits.LATA1
#define LEFT_BWD_TRIS TRISAbits.TRISA1

#define RIGHT_FWD_LAT LATAbits.LATA7
#define RIGHT_FWD_TRIS TRISAbits.TRISA7
#define RIGHT_BWD_LAT LATAbits.LATA6
#define RIGHT_BWD_TRIS TRISAbits.TRISA6

#define LED_LAT LATAbits.LATA0
#define LED_TRIS TRISAbits.TRISA0


// transfer types
#define WRITE_BURST_FLAG              0x40
#define READ_SINGLE_FLAG              0x80
#define READ_BURST_FLAG               0xC0

// number of frequency channels
#define NUMBER_OF_FCHANNELS      10

// arrays
#define CC1101_PATABLE           0x3E        // PATABLE address
#define CC1101_TXFIFO            0x3F        // TX FIFO address
#define CC1101_RXFIFO            0x3F        // RX FIFO address

// commands
#define CC1101_SRES              0x30        // Reset CC1101 chip
#define CC1101_SFSTXON           0x31        // Enable and calibrate frequency synthesizer (if MCSM0.FS_AUTOCAL=1). If in RX (with CCA):
                                             // Go to a wait state where only the synthesizer is running (for quick RX / TX turnaround).
#define CC1101_SXOFF             0x32        // Turn off crystal oscillator
#define CC1101_SCAL              0x33        // Calibrate frequency synthesizer and turn it off. SCAL can be strobed from IDLE mode without
                                             // setting manual calibration mode (MCSM0.FS_AUTOCAL=0)
#define CC1101_SRX               0x34        // Enable RX. Perform calibration first if coming from IDLE and MCSM0.FS_AUTOCAL=1
#define CC1101_STX               0x35        // In IDLE state: Enable TX. Perform calibration first if MCSM0.FS_AUTOCAL=1.
                                             // If in RX state and CCA is enabled: Only go to TX if channel is clear
#define CC1101_SIDLE             0x36        // Exit RX / TX, turn off frequency synthesizer and exit Wake-On-Radio mode if applicable
#define CC1101_SWOR              0x38        // Start automatic RX polling sequence (Wake-on-Radio) as described in Section 19.5 if
                                             // WORCTRL.RC_PD=0
#define CC1101_SPWD              0x39        // Enter power down mode when CSn goes high
#define CC1101_SFRX              0x3A        // Flush the RX FIFO buffer. Only issue SFRX in IDLE or RXFIFO_OVERFLOW states
#define CC1101_SFTX              0x3B        // Flush the TX FIFO buffer. Only issue SFTX in IDLE or TXFIFO_UNDERFLOW states
#define CC1101_SWORRST           0x3C        // Reset real time clock to Event1 value
#define CC1101_SNOP              0x3D        // No operation. May be used to get access to the chip status byte


// registers

#define CC1101_IOCFG2            0x00        // GDO2 Output Pin Configuration
#define CC1101_IOCFG1            0x01        // GDO1 Output Pin Configuration
#define CC1101_IOCFG0            0x02        // GDO0 Output Pin Configuration
#define CC1101_FIFOTHR           0x03        // RX FIFO and TX FIFO Thresholds
#define CC1101_SYNC1             0x04        // Sync Word, High Byte
#define CC1101_SYNC0             0x05        // Sync Word, Low Byte
#define CC1101_PKTLEN            0x06        // Packet Length
#define CC1101_PKTCTRL1          0x07        // Packet Automation Control
#define CC1101_PKTCTRL0          0x08        // Packet Automation Control
#define CC1101_ADDR              0x09        // Device Address
#define CC1101_CHANNR            0x0A        // Channel Number
#define CC1101_FSCTRL1           0x0B        // Frequency Synthesizer Control
#define CC1101_FSCTRL0           0x0C        // Frequency Synthesizer Control
#define CC1101_FREQ2             0x0D        // Frequency Control Word, High Byte
#define CC1101_FREQ1             0x0E        // Frequency Control Word, Middle Byte
#define CC1101_FREQ0             0x0F        // Frequency Control Word, Low Byte

// page 76
#define CC1101_MDMCFG4           0x10        // Modem Configuration
#define CC1101_MDMCFG3           0x11        // Modem Configuration
#define CC1101_MDMCFG2           0x12        // Modem Configuration
#define CC1101_MDMCFG1           0x13        // Modem Configuration
#define CC1101_MDMCFG0           0x14        // Modem Configuration
#define CC1101_DEVIATN           0x15        // Modem Deviation Setting
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

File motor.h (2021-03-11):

/*
 * 3 phase motor driver from an ESC
 *
 * Copyright (C) 2021 Adam Williams <broadcast at earthling dot net>
 * 
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
 */


#ifndef MOTOR_H
#define MOTOR_H



#ifdef __AVR__


#define F_CPU 16000000L

#include <inttypes.h>
#include <avr/io.h>
#include <avr/pgmspace.h>
#include <avr/interrupt.h>
#include <avr/wdt.h>
#include <util/delay.h>

#endif // __AVR__

#ifdef __x86_64__

#include  <stdint.h>

#endif // __x86_64__

#define bitRead(value, bit) (((value) >> (bit)) & 0x01)
#define bitSet(value, bit) ((value) |= (1UL << (bit)))
#define bitClear(value, bit) ((value) &= ~(1UL << (bit)))
#define bitToggle(reg, bit) ((reg) ^= (1 << (bit)))
#define bitWrite(value, bit, bitvalue) (bitvalue ? bitSet(value, bit) : bitClear(value, bit))
#define bitIsSet(value, bit) ((value) & (1UL << (bit)))
#define bitIsClear(value, bit) (!((value) & (1UL << (bit))))


#define CLAMP(x, y, z) ((x) = ((x) < (y) ? (y) : ((x) > (z) ? (z) : (x))))


// pins for the FETs
#define P_FET1	5
#define P_FET2	7
#define P_FET3	4
#define N_FET1	0
#define N_FET2	1
#define N_FET3	3

// use the PWM input pin for TX if no receive
#define TX_PIN 2
#define TX_PORT PORTD
#define TX_DDR DDRD



// the table played back by the interrupt handler
typedef struct
{
// members have to be volatile to be access by an interrupt handler
// time until the next interrupt
	volatile uint8_t time;
// value of the PORT register
	volatile uint8_t value;
} pwm_table_t;

// temporary table used for calculating the pwm table
typedef struct
{
// time since overflow
	int16_t time;
// Ps to turn off
	uint8_t p_mask;
// Ns to turn on
	uint8_t n_mask;
} event_table_t;


// need 9uS of deadband from P to N
//#define DEADBAND 104  // prescaler 1
//#define DEADBAND 12 // prescaler 2 with 18A Hobbyking
#define DEADBAND 128 // prescaler 2 with 35A Hobbyking

#define DEADBAND2 0 // minimum delay from N to P saves 20mA on 35A

// tweek this to get the right Hz
// need multiple padding events or higher power if period is too high
//#define PERIOD 582  // maximum before overflow prescaler 1 16khz
#define PERIOD 216  // prescaler 2 8khz
//#define PERIOD 108  // prescaler 2 16khz
//#define PERIOD 280  // prescaler 2 6khz


#define MAX_POWER ((int16_t)PERIOD)

#define MIN_POWER 1


void delayMicroseconds(unsigned int us);




#endif

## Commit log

2017-11-06 throttle minimums to avoid breaking oscillation. 150Hz PWM
    [SettingsWin.java, Truck.java]
2017-11-11 avoid I windup. Bluetooth workaround
    [SettingsWin.java, Truck.java]
2018-02-09 D feedback. PID limits. Heading widget
    [fuse.sch]
2018-02-10 highpass filter tester
2021-04-10 Reverse steering reversed. New tires. I2C fix. Amplified remote control.
    [bumper.FCStd, car_receive.X.production.obj, cring.FCStd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]
2021-05-21 Radio bugs. New tire. New camera bearing which doesn't require removing the handle.
    [clamp.stl, front_tire2.FCStd, gopro_bearing.FCStd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]
2021-06-12 Flash filesystem. Runtime motor calibration. Smaller motor mount.
    [motor2.FCStd, motor3.FCStd, rear_tire2.FCStd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]
2021-10-02 Captive locknut motor plate. Configuration for remote ADC.
    [car_remote.FCStd, clamp.stl, cring.FCStd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]
2022-01-25 New bumper design. Camera board ingests commands from a subject tracker.
    [bumper.FCStd]
2022-02-26 Moved camera parts to truckcam. Updated rear wheel.
    [cam_gearbox2.FCStd, gopro_bearing.FCStd, rear_tire3.FCStd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]
2022-05-04 Limit suspension travel.
    [steering.FCStd]
2022-06-20 phone holster. Magnet cover update. Front suspension update.
    [phone4.FCStd, steering.FCStd]
2022-08-30 anti static wheels
    [front_wheel.FCStd, traction.FCStd]
2022-10-16 brushless servo hack
    [F330_Blinky.OBJ, light.FCStd, motor.OBJ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]
2022-11-16 PLA steering fork. Antler update
    [antler2.FCStd, steering.FCStd]
2022-11-25 motor sign. container patches. smart leash.
    [leash4.FCStd]
2023-01-09 Radio using Si4463
    [car_remote2.FCStd]
2023-03-01 Leash enclosure. Remote update. Jetson nano enclosure
    [car_remote.FCStd, car_remote2.FCStd, charger2.FCStd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]
2023-03-01 captive nuts. Space for wheel fork
    [front_wheel.FCStd]
2023-05-19 ttyACM for camera panner
2023-06-04 leash PID. Final nose. USB panner
    [nose2.FCStd, steering.FCStd]
2023-06-12 power protector
    [cam_remote2.FCStd, car_remote2.FCStd, tool2.FCStd]
2023-06-20 new gopro mount
    [gopro_case2.FCStd]
2023-07-04 Stick drift configuration
    [cam_remote2.FCStd, car_remote2.FCStd, gopro_case.FCStd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]
2023-07-30 Container revision. Auto center sticks.
    [corners.FCStd, front_corner2.stl, radio_box2.FCStd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]
2023-09-27 Motion control for camera panner. Motor debugging table. Auto centering camera remote. Bigger electronical panel.
    [car_remote3.FCStd, front_wheel.FCStd, handle.FCStd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]
2023-10-06 taper maximum speed as leash angle increases
    [front_tire4.FCStd, offroad.stl]
2023-11-26 Leash feedback uses XY instead of angle/distance. Latest models.
    [antler3.FCStd, antler4.FCStd, bottom_corner.FCStd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]
2023-12-12 Cam frequency pattern crosstalk fixed. Brake button.
    [cam.c]
2023-12-23 New antler holders. Use odometry instead of throttle input to determine steering feedback.
    [antler4.FCStd]
2024-01-23 ball bearing leash. Hall effect angle sensor
    [corners.FCStd, leash11.FCStd, leash9.FCStd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]
2024-02-19 More robust offroad tire. Manual motor control.
2024-03-31 dummy battery hole
    [gopro_to_wood.FCStd]
2024-05-24 433Mhz migration
    [cam_remote2.FCStd, car_remote3.FCStd, gopro.FCStd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]
2024-11-03 Leash curve. ADC clamp
    [bumper.FCStd, car_remote3.FCStd, leash11.FCStd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]
2024-11-07 rear view glasses. Keep leash offset during power down
    [glasses.FCStd]
2024-11-09 leash tuning. Filter plotter. Motor sliders.
2024-12-20 speaker mount. steering caster.
    [antler5.FCStd, gopro4_to_wood.FCStd, gopro_to_wood.FCStd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]
2025-03-27 leash latch sensor
    [bumper.FCStd, leash13.FCStd, lid.FCStd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]
2025-06-05 corrupt config file indication. CLAMP bug.
    [car_remote3.FCStd, leash13.FCStd]
2025-08-22 UWB test. splash boards
2025-09-09 Leash settings. Wide drogue
    [trailer9.FCStd]
2026-02-23 Freewheeling modes. Tail light update.
    [antler5.FCStd, bumper2.FCStd, car_remote3.FCStd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]
2026-03-07 motor timing. Encoder magnet
    [leash13.FCStd, motor4.FCStd]
2026-04-03 PWM modulation, 100kbit
    [car_remote3.FCStd, motor4.FCStd]
2026-04-05 20kbit 45Hz
2026-04-14 new car remote
    [car_remote4.FCStd, charger3.FCStd]
2026-05-04 16 bit leash angle. New lid
    [car_remote4.FCStd, rear_light2.FCStd]
2026-05-07 Powered brake in RC mode
